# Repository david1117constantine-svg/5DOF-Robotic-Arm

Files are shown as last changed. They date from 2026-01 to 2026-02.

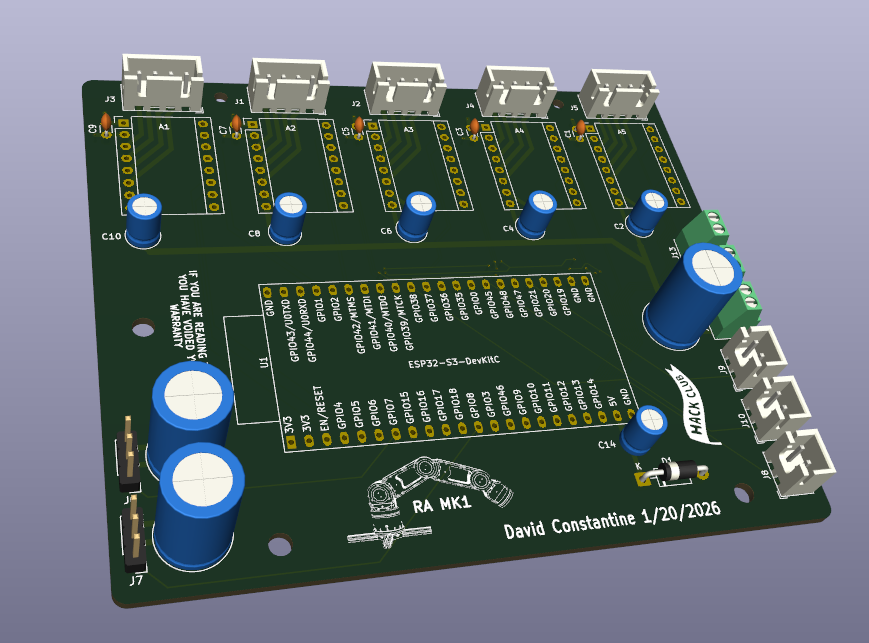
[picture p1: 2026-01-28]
Images/Screenshot 2026-01-27 141930.png

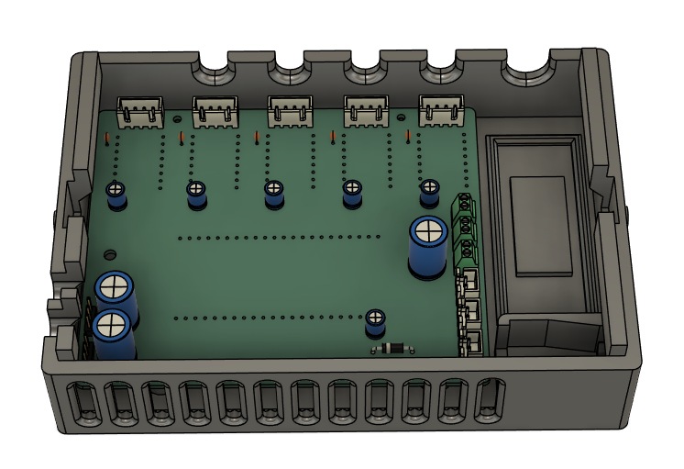
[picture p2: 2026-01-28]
Images/Screenshot 2026-01-28 093712.png

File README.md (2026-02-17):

# 5DOF-Robotic-Arm

This repository is for my very first Hack Club Blueprint Grant Submission, along with anyone else who wants to watch my progress and build their own 5DOF robot arm.



## Overview
* ESP32-S3
* A4988 Drivers
* Nema 17 Stepper Motors
* 25:1 Strain Wave Gearbox *Credit to @user_454693624 over on Makerworld (More Details in CAD Directory)*

## WHY?
This is the first passion project of mine that I have actually pursued. I love engineering, building computers, and 3d printing. All these hobbies have led to this monstrosity of an endeavour. This arm is meant to be modular, easily printable, and fairly inexpensive for hobbyists to build on their own and tinker with. This project has definitely challenged me in ways I couldn't imagine. I started, naive to the oncoming money pit that the thing would become. That's why I am so thankful to the amazing folks over at Blueprint and Hackclub for supporting students in their pursuit of engineering.

## How Does it Work?
This 5DOF Arm is powered by 5 NEMA 17 34mm 0.35A 12V 1.8deg Stepper Motors that you can find at many online stores, such as StepperOnline or, in my case, Adafruit. The joints in the shoulder, elbow, and wrist pitch axis all use the same gearbox and housing assemblies, making for simpler printing and a common attachment point for new structural designs. You might notice there is no end effector piece on this Arm, and that is intentional. The PCB has two servo headers that can be utilized for many different Griper or Claw style designs, or maybe a suction cup or magnet, who knows the possibilities. The PCB is also made for simple installations, simply requiring you to insert your ESP32, motor drivers, servos, etc.

## How To Use It?
One of the major design philosophies behind this project was to build a platform that could be used to test different control mechanisms. As I wrote in the blueprint submission page, I plan to attempt control with a BCI device if I can get my hands on one. To set up the arm, compile and upload the firmware with Arduino IDE, and plug the board into the PCB. I suggest running the code over USB to get a serial output, this will provide you with an IP which you can go to and control the Arm over wifi with the device of your choice. *Note you must replace the SSID and PASSWORD fields with your wifi credentials to let the board connect to wifi. The web GUI is fairly straightforward with multiple ways of interacting with the arm, whether that be individual joint movements or Cartesian Coordinates, though the IK solver has not been refined enough yet for that system to work as intended.

## PCB: Schematic, Footprints, and Renders

#### Schematic:


#### Footprint:


#### Render:


## More Photos:











## BOM
| Item | Quantity | Total Price ($) | Link |
|:---|:---|:---|:---|
| Self-Sourced | | | |
| Screws - Assorted M3 | 2240 | Self-Sourced | |
| Bearing - 6807 2RS | 5 | Self-Sourced | [Link](https://www.amazon.com/XIKE-6807-2RS-Bearings-35x47x7mm-Pre-Lubricated/dp/B09D2ZHNPH/ref=sr_1_4) |
| Microcontroller - ESP32 | 1 | Self-Sourced | [Link](https://www.aliexpress.us/item/3256809776335245.html) |
| Electronics (Exluding PCB) | | | |
| Stepper motor - NEMA-17 size - 200 steps/rev, 12V 350mA | 5 | 70.00 | [Link](https://www.google.com/search?q=NEMA+17+stepper+motor) |
| Stepper Motor Driver - A4988 | 5 | 3.66 | [Link](https://www.aliexpress.us/item/3256808219893938.html) |
| Limit Switch | 3 | 0.41 | [Link](https://www.lcsc.com/product-detail/C50395955.html) |
| Buck Converter - 12v to 5v, 5A | 1 | 2.98 | [Link](https://www.aliexpress.us/item/3256810527502423.html) |
| Wire Connectors - JST xh 2.54 2Pin 10pcs | 1 | 1.39 | [Link](https://www.aliexpress.us/item/3256808413328991.html) |
| Wire Connectors - JST xh 2.54 4Pin 10pcs | 1 | 1.86 | [Link](https://www.aliexpress.us/item/3256808413328991.html) |
| Wire - General Purpose 28 Gauge Wire | 1 | 9.28 | [Link](https://www.aliexpress.us/item/3256805264336680.html) |
| Heat Shrink Tubing - 5mm ID, 5M | 1 | 3.28 | [Link](https://www.aliexpress.us/item/3256806019046145.html) |
| Power Supply - DC12V 8A | 1 | 15.43 | [Link](https://www.aliexpress.us/item/3256801543468653.html) |
| Hardware | | | |
| Extrutions - 150mm 2020 T-slot Extrutions 4pcs | 4 | 18.05 | [Link](https://www.aliexpress.us/item/3256808366074196.html) |
| Screws - M4x10 Countersunk | 4 | 0.02 | [Link](https://jlcmc.com/product/s/E02/EDLJ/din-7991-gb-t-70.3-hex-socket-countersunk-head-screw) |
| Screws - M4x16 BHCS | 8 | 0.09 | [Link](https://jlcmc.com/product/s/E02/EDLG/iso-7380-hex-socket-button-head-screw) |
| T-Nuts - M4 20 Series Profile | 12 | 0.09 | [Link](https://jlcmc.com/product/s/T02/TPAA/m3-m4-m5-t-nut-20-series-aluminum-profile-fasteners) |
| Heat Inserts - M3x4x5 | 100 | 4.18 | [Link](https://www.aliexpress.us/item/3256807712431371.html) |
| NEMA 17 Strain Wave Gearbox (OpenSource) BOM | | | [Link](https://makerworld.com/en/models/1303481-nema-17-strain-wave-gearbox#profileId-1336298) |
| Bearings  - 6706 2RS | 5 | 4.35 | [Link](https://www.aliexpress.us/item/3256806677694798.html) |
| Bearings - 605ZZ | 10 | 0.99 | [Link](https://www.aliexpress.us/item/3256801622664412.html) |
| Bearings - 4mm Balls | 200 | 6.28 | [Link](https://www.aliexpress.us/item/3256807297992129.html) |
| PCB Components | | | |
| Capacitor - 100uF 16V Capacitor | 5 | 0.70 | [Link](https://www.lcsc.com/product-detail/C31190.html) |
| Capacitor - 0.1uF Capacitor | 5 | 0.67 | [Link](https://www.lcsc.com/product-detail/C1620282.html) |
| Capacitor - 47uF | 1 | 0.90 | [Link](https://www.lcsc.com/product-detail/C3540.html) |
| Capacitor - 1000uF | 2 | 1.33 | [Link](https://www.lcsc.com/product-detail/C31154.html) |
| Screw Terminal - 2 Pin | 3 | 1.04 | [Link](https://www.aliexpress.us/item/2251832049646879.html) |
| Schottky Diode - 1N5819 | 2 | 0.06 | [Link](https://www.lcsc.com/product-detail/C2132.html) |
| Female Pin Headers - 1x22 | 2 | 0.80 | [Link](https://www.lcsc.com/product-detail/C474775.html) |
| Female Pin Headers - 1x8 | 10 | 0.59 | [Link](https://www.aliexpress.us/item/3256804116522266.html) |

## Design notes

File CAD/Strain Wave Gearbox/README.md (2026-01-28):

# Credit to user_454693624 over on Makerworld for the Strain-Wave Gearbox design!

### You can find the files for the gearbox design at this link:
https://makerworld.com/en/models/1303481-nema-17-strain-wave-gearbox#profileId-1336298
------
The CAD in this repository contains two modified components of user_454693624's design. First is the Output Hub. I have included this piece in this folder as I needed to extend the hub and change the mounting to threaded inserts. The second modified part is the Cap, which you will find combined in the frames of the Upper Arm, Forearm, and Wrist components.

Again, thank you to user_454693624 for giving me permission to use their design and go check it out!

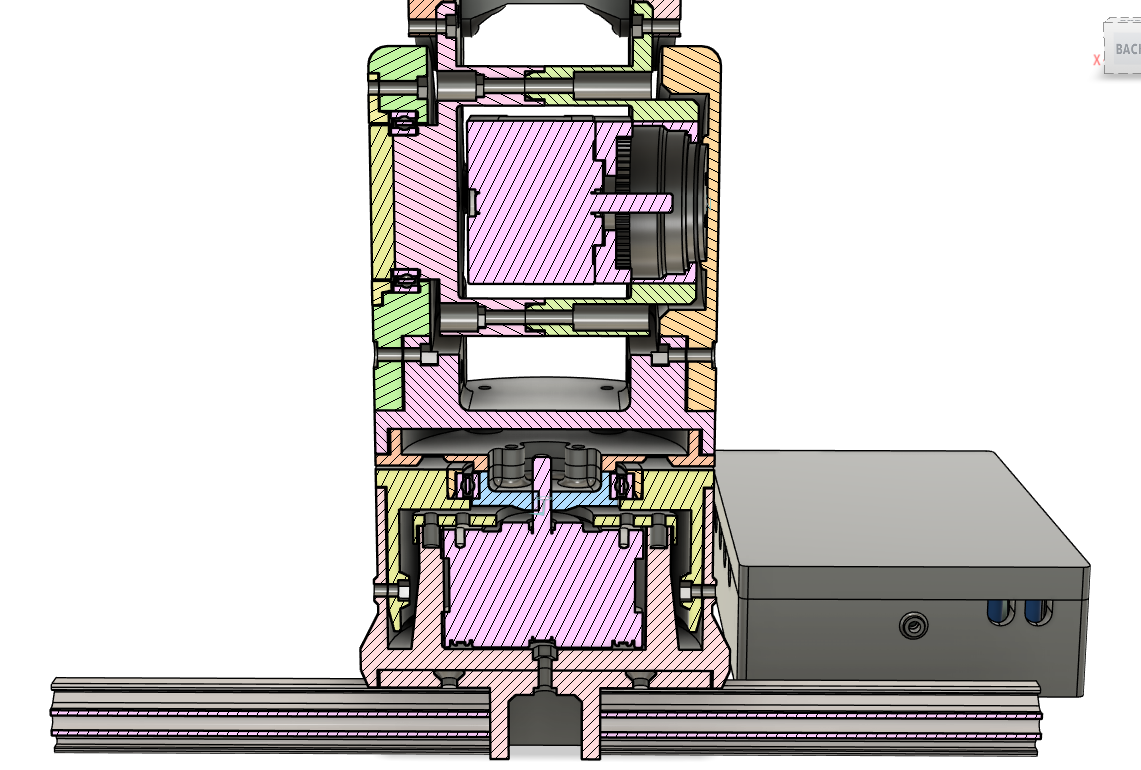
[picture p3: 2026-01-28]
Images/Screenshot 2026-01-28 104803.png

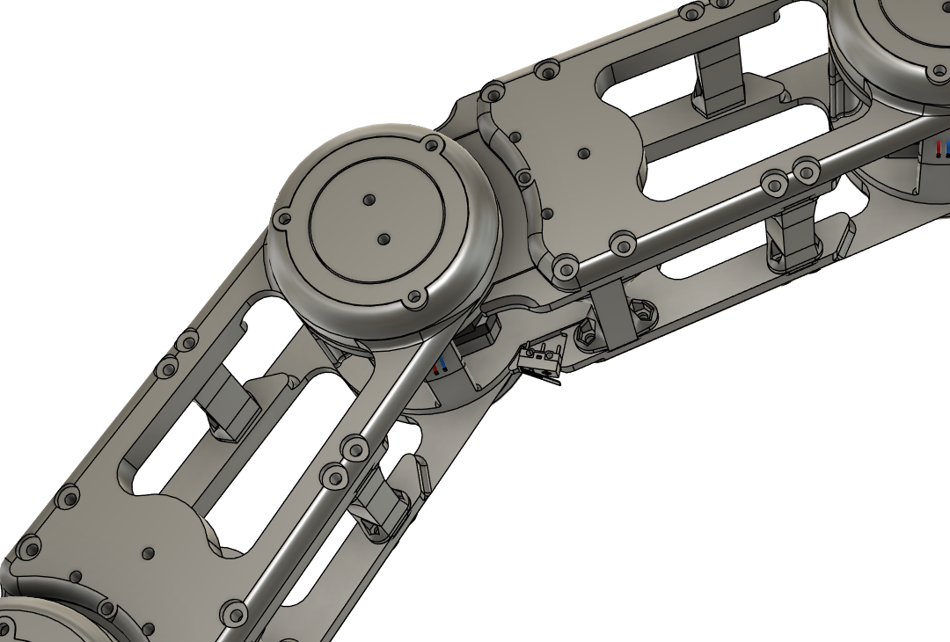
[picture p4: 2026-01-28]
Images/Screenshot 2026-01-28 140131.png

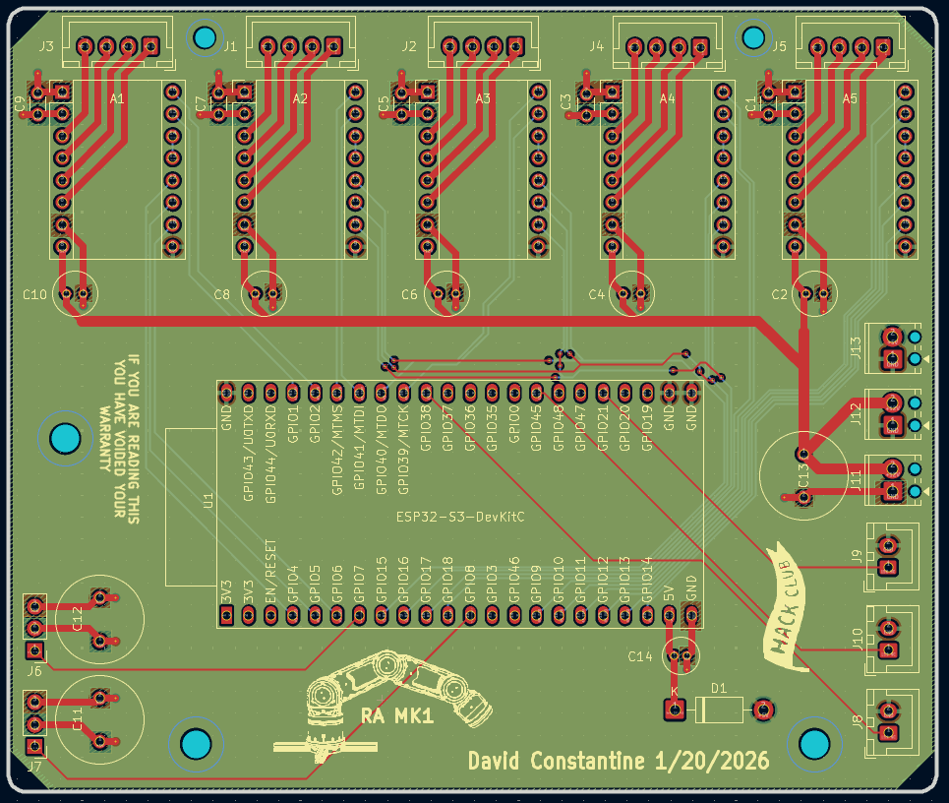
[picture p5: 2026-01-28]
Images/Screenshot 2026-01-27 141817.png

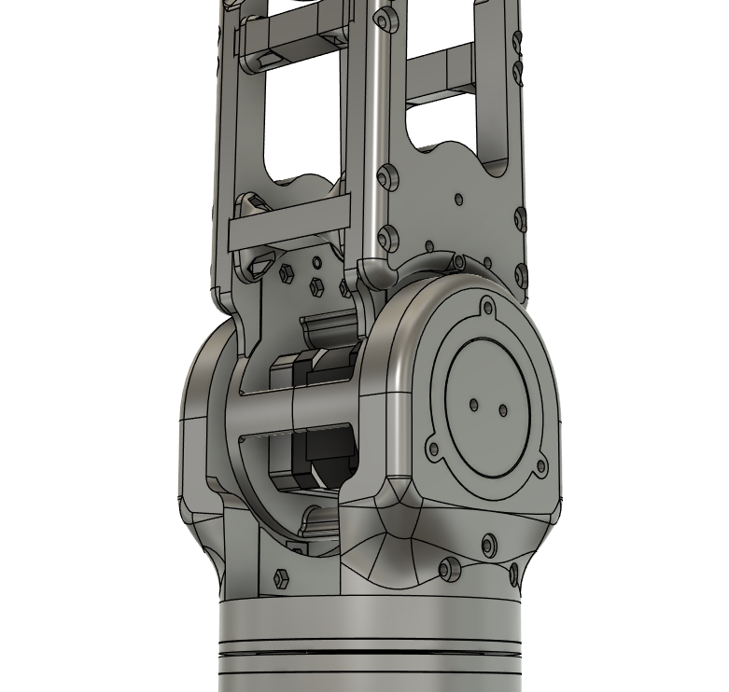
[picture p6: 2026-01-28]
Images/Screenshot 2026-01-28 140021.png

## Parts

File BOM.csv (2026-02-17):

Item | Description | Quantity | Unit Price ($) | Total Price ($) | URL | Running Total ($ with Tax)
Self-Sourced
Screws - Assorted M3 | Screws for general building of the arm, 2440 just came in the box, havent used them all. | 2240 | N/A | Self-Sourced |  | 0.00
Bearing - 6807 2RS | Bearings, 47mm OD, 35mm ID, 7mm Thickness. 6pck on aliexpress seemed to be the cheapest price, though that is on sale so if you are reading this and it is no longer on sale anymore, there is an amazon link with a constant 15.99 price, which I actually sourced. | 5 | N/A | Self-Sourced | https://www.amazon.com/XIKE-6807-2RS-Bearings-35x47x7mm-Pre-Lubricated/dp/B09D2ZHNPH https://www.aliexpress.us/item/3256808547952086.html?curPageLogUid=aeOEVXLjXg1Q | 0.00
Microcontroller - ESP32 | Most ESP32 variants should do as long as they have 36 or more GPIO pins. In this example I am using an ESP32-S3 N18R8 | 1 | N/A | Self-Sourced | https://www.aliexpress.us/item/3256809776335245.html?curPageLogUid=GRDrdkb15ClS | 0.00
Electronics (Exluding PCB)
Stepper motor - NEMA-17 size - 200 steps/rev, 12V 350mA | 4 Wire, 1.8Deg per Step, with 20 N*cm of torque per phase at a max current of 350mAh (0.35A). RoHS certified. | 5 | 14.00 | 70.00 | Stepper motor - NEMA-17 size - 200 steps/rev, 12V 350mA | 75.25
Stepper Motor Driver - A4988 | Stepper Motor Driver, 1.2A, 5 Step resolutions, Adjustable maximum current output. Overheat Thermal shutdown and crossover-current protection. Comes in a pack of 5 for the cheapest sourcing price included both amazon link that had a stable price of 10.19. along with an aliexpress link which often goes on sale for cheaper but can sometimes be 13.95. The price listed is the aliexpress link while on sale | 5 | 0.73 | 3.66 | Amazon.com: A4988 Stepper Motor Driver https://www.aliexpress.us/item/3256808219893938.html?curPageLogUid=ozd9t4rogPcP | 79.18
Limit Switch | Minimum quantity on LCSC was 5, as usual | 3 | 0.08 | 0.41 | https://www.lcsc.com/product-detail/C50395955.html | 79.62
Buck Converter - 12v to 5v, 5A | Buck converter to step down the 12v for the steppers to 5v for the other electronics like the esp and the drivers. | 1 | 2.98 | 2.98 | https://www.aliexpress.us/item/3256810527502423.html?curPageLogUid=wrW3I3VnBbO7 | 82.82
Wire Connectors - JST xh 2.54 2Pin 10pcs | Connectors for the Limit Switches | 1 | 1.39 | 1.39 | https://www.aliexpress.us/item/3256808413328991.html?mp=1 | 84.31
Wire Connectors - JST xh 2.54 4Pin 10pcs | Connectors for the steppers, will allow for much easier building and protoyping | 1 | 1.86 | 1.86 | https://www.aliexpress.us/item/3256808413328991.html?mp=1 | 86.31
Wire - General Purpose 28 Gauge Wire | Wire for extention cables for the Stepper Motors | 1 | 9.28 | 9.28 | https://www.aliexpress.us/item/3256805264336680.html | 96.29
Heat Shrink Tubing - 5mm ID, 5M | For all the soldered joints to be electrically insulated | 1 | 3.28 | 3.28 | https://www.aliexpress.us/item/3256806019046145.html?mp=1 | 99.82
Power Supply - DC12V 8A | Power Supply for the arm | 1 | 15.43 | 15.43 | https://www.aliexpress.us/item/3256801543468653.html?mp=1 | 116.41
Hardware
Extrutions - 150mm 2020 T-slot Extrutions 4pcs | Extrutions for the base of the arm. Will allow for the arm to be mounted almost anywhere or stand alone when the end effector is within a certain radius. | 4 | 4.51 | 18.05 | https://www.aliexpress.us/item/3256808366074196.html?curPageLogUid=zHtV8X7rHrXA | 135.81
Screws - M4x10 Countersunk | Countersunk M4 screws for connecting the extrutions to Robot Base | 4 | 0.0043 | 0.02 | https://jlcmc.com/product/s/E02/EDLJ/din-7991-gb-t-70.3-hex-socket-countersunk-head-screw | 135.83
Screws - M4x16 BHCS | BHCS M4 screws for connecting the extrutions to the base | 8 | 0.0111 | 0.09 | https://jlcmc.com/product/s/E02/EDLG/iso-7380-hex-socket-button-head-screw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 | 135.93
T-Nuts - M4 20 Series Profile | T-Nuts for connecting extrutions to robot base | 12 | 0.0075 | 0.09 | https://jlcmc.com/product/s/T02/TPAA/m3-m4-m5-t-nut-20-series-aluminum-profile-fasteners | 136.03
Heat Inserts - M3x4x5 | Need some more for the design | 100 | 0.0418 | 4.18 | https://www.aliexpress.us/item/3256807712431371.html?curPageLogUid=NFashz8ytky9 | 140.52
NEMA 17 Strain Wave Gearbox (OpenSource) BOM |  |  |  |  | https://makerworld.com/en/models/1303481-nema-17-strain-wave-gearbox#profileId-1336298
Bearings - 6706 2RS |  | 5 | 0.87 | 4.35 | https://www.aliexpress.us/item/3256806677694798.html?curPageLogUid=v6HSvHcuK7CU | 145.20
Bearings - 605ZZ |  | 10 | 0.1 | 0.99 | https://www.aliexpress.us/item/3256801622664412.html?curPageLogUid=edU8vGmWTP8q | 146.26
Bearings - 4mm Balls |  | 200 | 0.0314 | 6.28 | https://www.aliexpress.us/item/3256807297992129.html?curPageLogUid=DUdxTNKNhLz3 | 153.01
PCB Components
Capacitor - 100uF 16V Capacitor | Minimum quantity was 50 on LCSC | 5 | 0.014 | 0.70 | https://www.lcsc.com/product-detail/C2960196.html?s_z=n_100uf%2520capacitor | 153.76
Capacitor - 0.1uF Capacitor | Minimum quantity was 5 on LCSC | 5 | 0.1347 | 0.67 | https://www.lcsc.com/product-detail/C1620282.html | 154.48
Capacitor - 47uF | Comes in 20pcs on Aliexpress, cheaper than LCSC surprisingly | 1 | 0.045 | 0.90 | https://www.aliexpress.us/item/3256804117722266.html?curPageLogUid=qXib9S2fzA2W | 155.45
Capacitor - 1000uF | Comes in 20pcs on Aliexpress, couldnt find on LCSC | 2 | 0.0665 | 1.33 | https://www.aliexpress.us/item/3256804117722266.html?curPageLogUid=qXib9S2fzA2W | 156.88
Screw Terminal - 2 Pin | Comes in 5pcs on Aliexpress | 3 | 0.208 | 1.04 | https://www.aliexpress.us/item/3256807006502215.html?curPageLogUid=ZN9fxmU7svuY | 158.00
Schottky Diode - 1N5819 | Got 2 because knowing me I'm gonna break one soldering | 2 | 0.03 | 0.06 | https://www.lcsc.com/product-detail/C2906661.html | 158.06
Female Pin Headers - 1x22 | For the ESP32 | 2 | 0.4014 | 0.80 | https://www.lcsc.com/product-detail/C20071202.html | 158.92
Female Pin Headers - 1x8 | For A4988 Drivers | 10 | 0.0585 | 0.59 | https://www.lcsc.com/product-detail/C429957.html | 159.55

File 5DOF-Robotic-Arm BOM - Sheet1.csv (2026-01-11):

Item | Description | Quantity | Unit Price ($) | Total Price ($) | URL | Running Total ($ with Tax)
Bearing - 6807 2RS | Bearings, 47mm OD, 35mm ID, 7mm Thickness. 6pck on aliexpress seemed to be the cheapest price, though that is on sale so if you are reading this and it is no longer on sale anymore, there is an amazon link with a constant 15.99 price, which I actually sourced. | 5 | N/A | Self-Sourced | https://www.amazon.com/XIKE-6807-2RS-Bearings-35x47x7mm-Pre-Lubricated/dp/B09D2ZHNPH https://www.aliexpress.us/item/3256808547952086.html?curPageLogUid=aeOEVXLjXg1Q | 0.00
Microcontroller - ESP32 | Most ESP32 variants should do as long as they have 36 or more GPIO pins. In this example I am using an ESP32-S3 N18R8 | 1 | N/A | Self-Sourced | https://www.aliexpress.us/item/3256809776335245.html?curPageLogUid=GRDrdkb15ClS | 0.00
Stepper motor - NEMA-17 size - 200 steps/rev, 12V 350mA | 4 Wire, 1.8Deg per Step, with 20 N*cm of torque per phase at a max current of 350mAh (0.35A). RoHS certified. | 5 | 14.00 | 70.00 | Stepper motor - NEMA-17 size - 200 steps/rev, 12V 350mA | 75.25
Stepper Motor Driver - A4988 | Stepper Motor Driver, 1.2A, 5 Step resolutions, Adjustable maximum current output. Overheat Thermal shutdown and crossover-current protection. Comes in a pack of 5 for the cheapest sourcing price included both amazon link that had a stable price of 10.19. along with an aliexpress link which often goes on sale for cheaper but can sometimes be 13.95. The price listed is the aliexpress link while on sale | 5 | 1.18 | 5.90 | Amazon.com: A4988 Stepper Motor Driver https://www.aliexpress.us/item/3256808219893938.html?curPageLogUid=ozd9t4rogPcP | 81.59
Buck Converter - 12v to 5v | Buck converter to step down the 12v for the steppers to 5v for the other electronics like the esp and the drivers. | 1 | 1.69 | 1.69 | https://www.aliexpress.us/item/3256805964919227.html?curPageLogUid=Vf5B1UHJQ9oe | 83.41
Wire Connectors - JST xh 2.54 5Pin 10pcs | Connectors for the steppers, will allow for much easier building and protoyping | 1 | 2.31 | 2.31 | https://www.aliexpress.us/item/3256808501357728.html?curPageLogUid=yp1VBhINy1jJ | 85.89
Power Supply - DC12V 5A | Power Supply for the arm. Comes with EU plug, but I have so many C14 power cables it isnt funny. Should not be a problem. | 1 | 8.32 | 8.32 | https://www.aliexpress.us/item/3256810479010704.html?curPageLogUid=Aaaj8G0MkgZc | 94.83
Extrutions - 150mm 2020 T-slot Extrutions 4pcs | Extrutions for the base of the arm. Will allow for the arm to be mounted almost anywhere or stand alone when the end effector is within a certain radius. | 1 | 17.96 | 17.96 | https://www.aliexpress.us/item/3256808366074196.html?curPageLogUid=zHtV8X7rHrXA | 114.14
Screws - M4x10 Countersunk | Countersunk M4 screws for connecting the extrutions to Robot Base | 4 | 0.0043 | 0.02 | https://jlcmc.com/product/s/E02/EDLJ/din-7991-gb-t-70.3-hex-socket-countersunk-head-screw | 114.16
Screws - M4x16 BHCS | BHCS M4 screws for connecting the extrutions to the base | 8 | 0.0111 | 0.09 | https://jlcmc.com/product/s/E02/EDLG/iso-7380-hex-socket-button-head-screw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 | 114.26
T-Nuts - M4 20 Series Profile | T-Nuts for connecting extrutions to robot base | 12 | 0.0075 | 0.09 | https://jlcmc.com/product/s/T02/TPAA/m3-m4-m5-t-nut-20-series-aluminum-profile-fasteners | 114.36
Wire - General Purpose 28 Gauge Wire | Wire for extention cables for the Stepper Motors | 1 | 9.66 | 9.66 | https://www.aliexpress.us/item/3256805264336680.html | 124.74
Sweep Dynamics Cycloidal BOM
Bearings - 6707 2RS |  | 10 | 1.97 | 19.75 | https://www.aliexpress.us/item/2255800723290638.html | 145.97
Bearings - MR137ZZ |  | 10 | 0.93 | 9.29 | https://www.amazon.com/uxcell-Miniature-Bearings-Appliances-Machinery/dp/B0D2LBCKP2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 | 155.96
Bearings - MR128 2RS |  | 10 | 1.00 | 10.01 | https://www.aliexpress.us/item/3256806709867700.html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 | 166.72
Rollers - M3x5mmx10mm | Only need 30 ordering 40 is cheapest | 40 | 0.22 | 8.78 | https://www.aliexpress.us/item/3256805776299657.html | 176.16
Screws - M3x20 BHCS |  | 30 | 0.0082 | 0.25 |  | 176.42
Screws - M3x8 Countersunk |  | 20 | 0.0032 | 0.06 |  | 176.49

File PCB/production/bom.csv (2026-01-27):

Designator | Footprint | Quantity | Value | LCSC Part #
A1, A2, A3, A4, A5 | Pololu_Breakout-16_15.2x20.3mm | 5 | Breakout_A4988
C1, C3, C5, C7, C9 | C_Disc_D3.0mm_W1.6mm_P2.50mm | 5 | 100nF
C10, C2, C4, C6, C8 | C_Radial_D5.0mm_H7.0mm_P2.00mm | 5 | 100uF
C11, C12, C13 | C_Radial_D10.0mm_H16.0mm_P5.00mm | 3 | 1000uF
C14 | C_Radial_D4.0mm_H7.0mm_P1.50mm | 1 | 47uF
D1 | D_DO-41_SOD81_P10.16mm_Horizontal | 1 | 1N5819
J1, J2, J3, J4, J5 | JST_XH_B4B-XH-A_1x04_P2.50mm_Vertical | 5 | JST XH 2.54 4Pin
J10 | JST_XH_B2B-XH-A_1x02_P2.50mm_Vertical | 1 | LS3
J11 | TerminalBlock_Phoenix_MPT-0,5-2-2.54_1x02_P2.54mm_Horizontal | 1 | 12Vin
J12 | TerminalBlock_Phoenix_MPT-0,5-2-2.54_1x02_P2.54mm_Horizontal | 1 | 12Vout
J13 | TerminalBlock_Phoenix_MPT-0,5-2-2.54_1x02_P2.54mm_Horizontal | 1 | 5Vin
J6 | PinHeader_1x03_P2.54mm_Vertical | 1 | Servo 1
J7 | PinHeader_1x03_P2.54mm_Vertical | 1 | Servo 2
J8 | JST_XH_B2B-XH-A_1x02_P2.50mm_Vertical | 1 | LS1
J9 | JST_XH_B2B-XH-A_1x02_P2.50mm_Vertical | 1 | LS2
U1 | ESP32-S3-DevKitC | 1 | ESP32-S3-DevKitC

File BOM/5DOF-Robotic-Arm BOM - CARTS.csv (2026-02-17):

Store/Website | Total | Shipping | Grand Total | Notes
JLCPC/JLCMC | $29.19 | $10.11 | $39.30
LCSC | $3.38 | $9.05 | $15.39 | Extra Fees: 3.00 Handling Fee + 0.04 discount?
AliExpress | $77.04 | $37.67 | $123.33 | Extra Fees: 8.62
Digikey | $70.00 | $6.99 | $76.99
 |  |  | $255.01

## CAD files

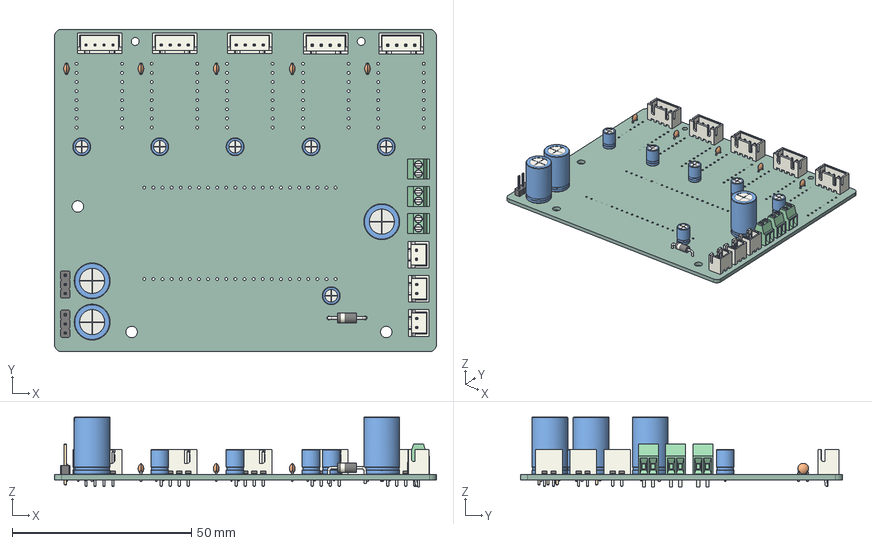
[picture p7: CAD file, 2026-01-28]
CAD/Electronics/5DOF-Robotic-Arm-PCB_MK2.5.step
106.5 x 89.9 x 19.5 mm
C_Disc_D3.0mm_W1.6mm_P2.50mm x 5
C_Radial_D10.0mm_H16.0mm_P5.00mm x 3
C_Radial_D5.0mm_H7.0mm_P2.00mm x 5
JST_XH_B4B-XH-A_1x04_P2.50mm_Vertical x 5
D_DO-41_SOD81_P10.16mm_Horizontal
TerminalBlock_Phoenix_MPT-0,5-2-2.54_1x02_P2.54mm_Horizontal x 3
JST_XH_B2B-XH-A_1x02_P2.50mm_Vertical x 3
PinHeader_1x03_P2.54mm_Vertical x 2
C_Radial_D4.0mm_H7.0mm_P1.50mm
5DOF-Robotic-Arm-PCB_MK2_PCB

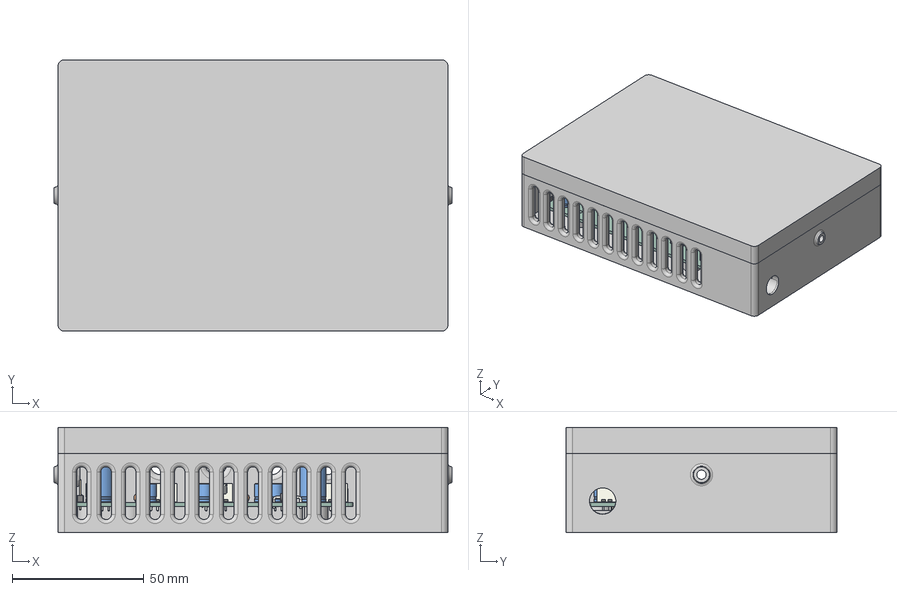
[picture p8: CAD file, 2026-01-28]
CAD/Electronics/Electronics Case/Electronics Case.step
151.0 x 103.0 x 40.0 mm
DC Barrel to Screw Terminal Adapter Fit Test
Electronics_Case
C_Disc_D3.0mm_W1.6mm_P2.50mm x 5
C_Radial_D10.0mm_H16.0mm_P5.00mm x 3
C_Radial_D5.0mm_H7.0mm_P2.00mm x 5
JST_XH_B4B-XH-A_1x04_P2.50mm_Vertical x 5
D_DO-41_SOD81_P10.16mm_Horizontal
TerminalBlock_Phoenix_MPT-0,5-2-2.54_1x02_P2.54mm_Horizontal x 3
JST_XH_B2B-XH-A_1x02_P2.50mm_Vertical x 3
PinHeader_1x03_P2.54mm_Vertical x 2
C_Radial_D4.0mm_H7.0mm_P1.50mm
5DOF-Robotic-Arm-PCB_MK2_PCB
Electronics_Case_Lid

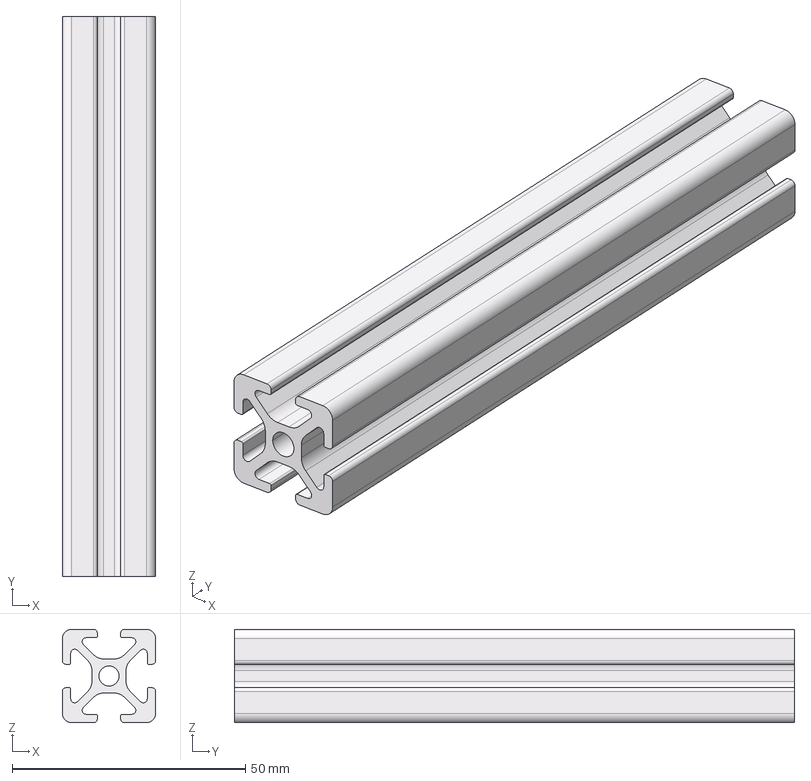
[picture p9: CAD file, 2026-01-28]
CAD/Extrution/item_37003_profile-5-20x20-natural-_120_high.step
20.0 x 120.0 x 20.0 mm

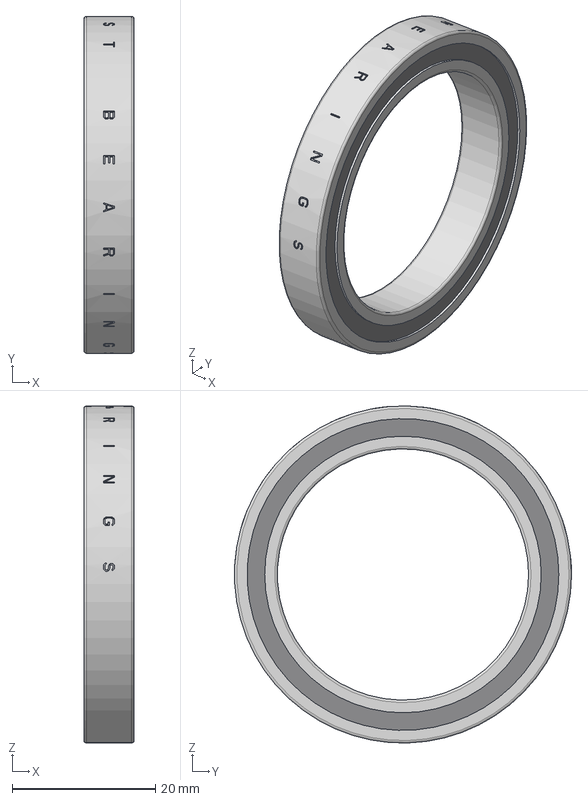
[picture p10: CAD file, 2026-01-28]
CAD/Misc Parts/AST_Bearings_6807-2RS.step
7.01 x 47.0 x 47.0 mm

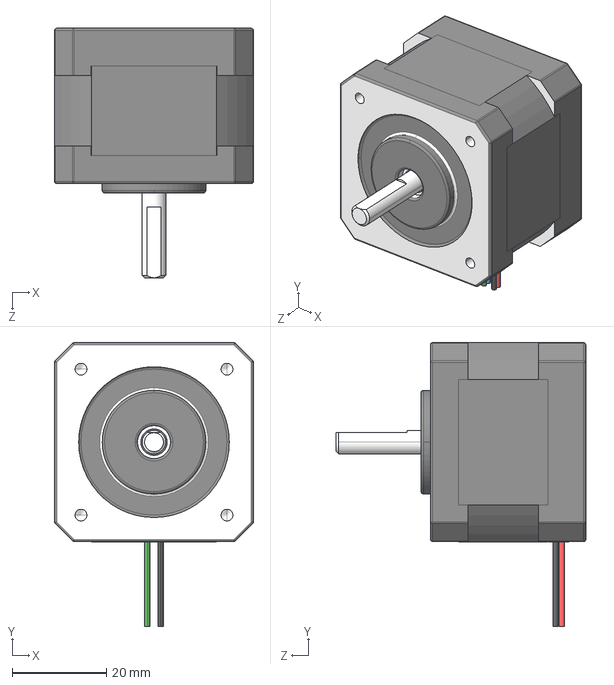
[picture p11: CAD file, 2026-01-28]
CAD/Nema 17 Motor/17HS13-0404S1.STEP
42.3 x 60.3 x 53.0 mm

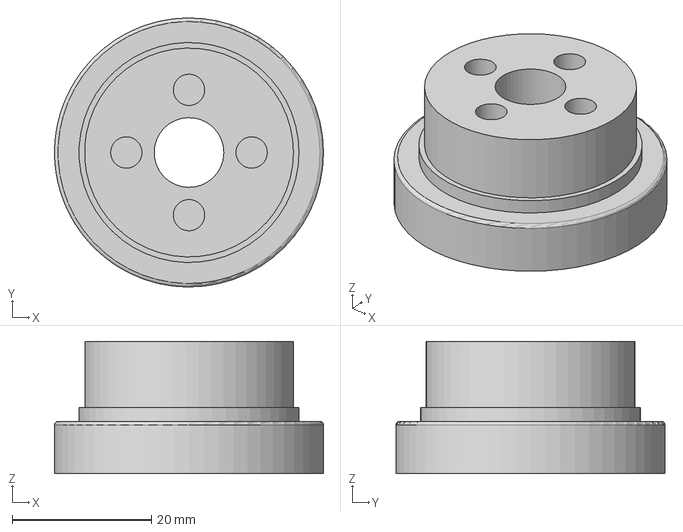
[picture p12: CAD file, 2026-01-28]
CAD/Strain Wave Gearbox/Output Hub.step
38.6 x 38.6 x 19.0 mm

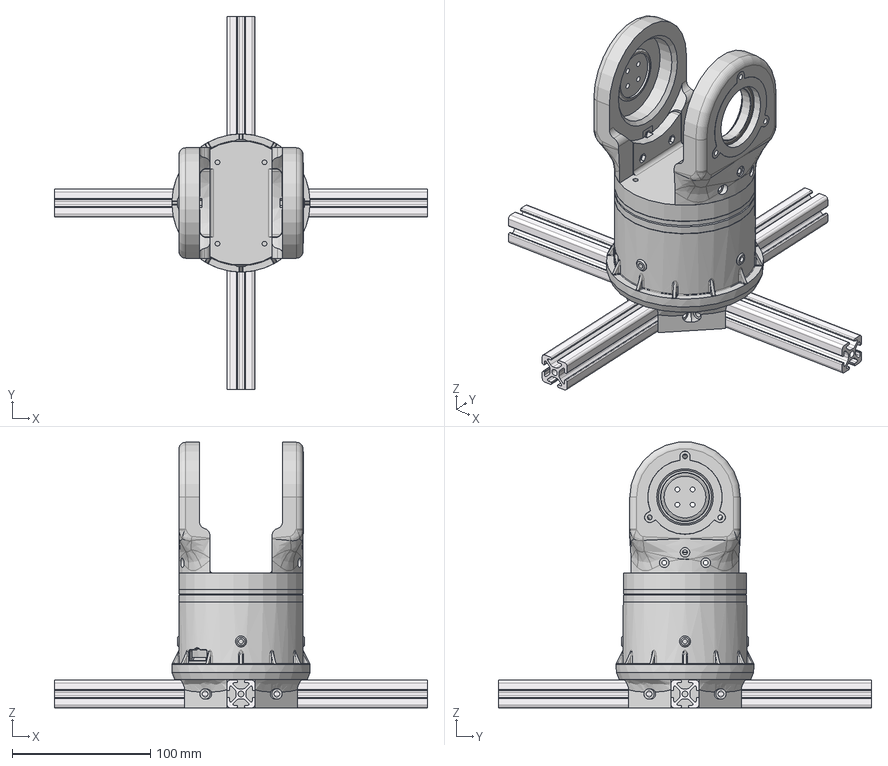
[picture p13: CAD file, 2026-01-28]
CAD/Waist + Shoulder/Robotic_Arm-Waist+Shoulder.step
270.0 x 270.0 x 192.3 mm
item_0037003_Profil 5 20x20_L=120_1 x 4
Base_ExtrusionConectors
Waist_Floor-Motor_Cap
Waise_FloorBearingCap
6807-2RS x 2
Waist_BearingTentionRing
Hip_WaistBeaaringBottom
Hip_WaistPlate
Hip_Hip-Arm_Base
Hip_Hip-Arm_Bearing-Arm
Hip_Hip-Arm_Bearing_Cover
Hip_Hip-Arm_Gear_Arm
17HS13-0404S1

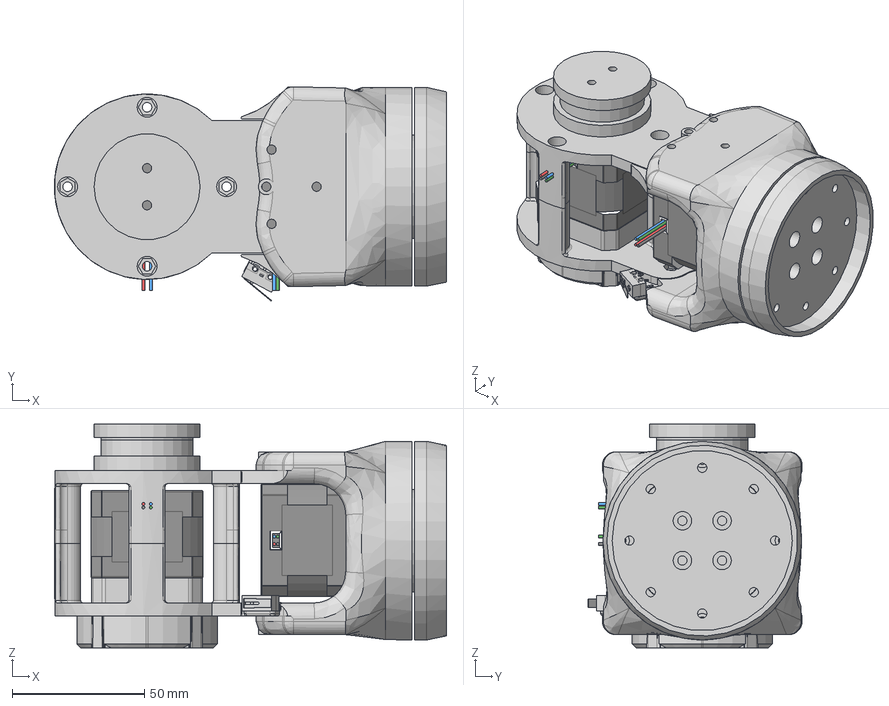
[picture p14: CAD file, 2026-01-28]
CAD/Wrist/Robotic_Arm-Wrist.step
147.9 x 80.9 x 84.5 mm
Cap
Upper_Arm-Bearingside
Upper_Arm-Bearing_Cover
Fixed Stator
17HS13-0404S1 x 2
Wrist_Frame
6807-2RS
Wrist_Bearing_Cap
Wrist_Rear_Bearing_Cap
Wrist_End_Effector_Mount
000021319_Simplify_1

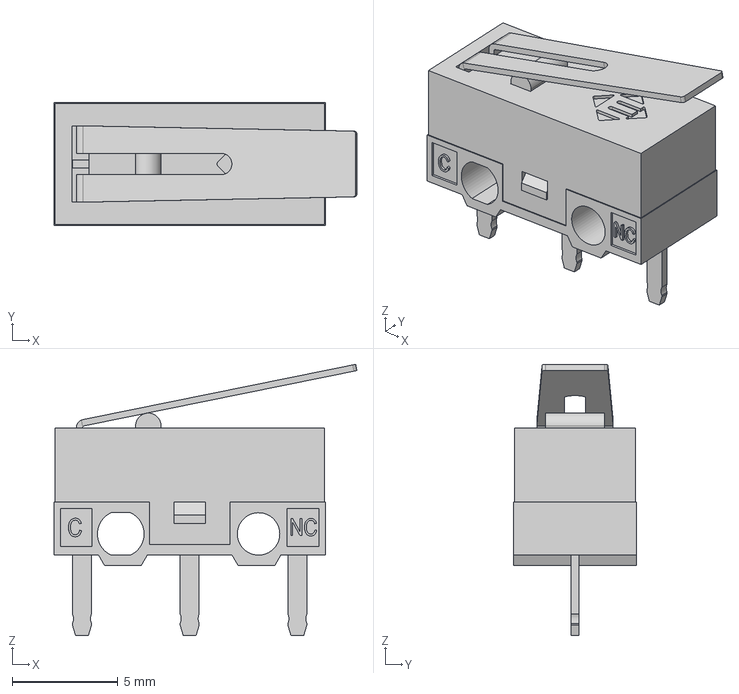
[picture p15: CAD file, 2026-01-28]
CAD/Misc Parts/SS075xx01FxxxP1A.step
14.3 x 5.80 x 12.8 mm

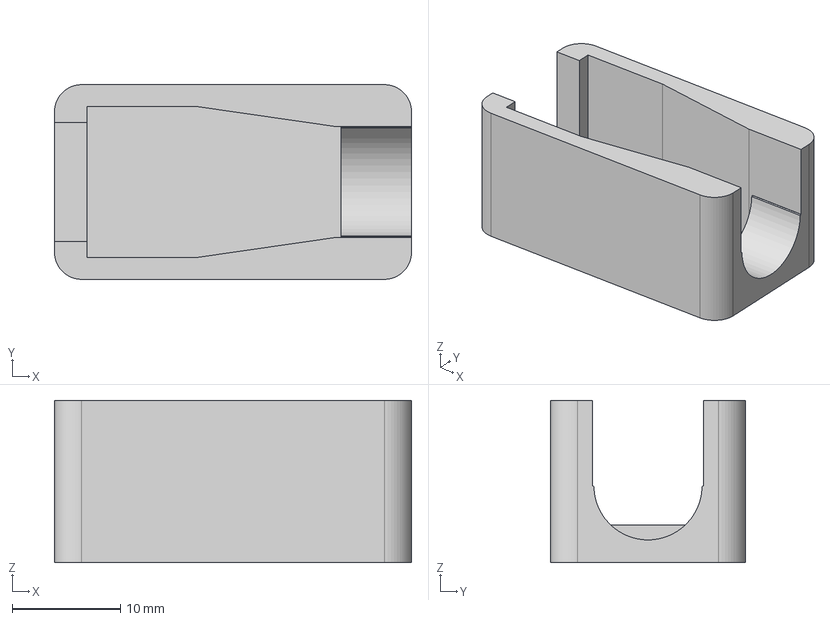
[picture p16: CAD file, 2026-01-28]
CAD/Electronics/Barrel to Screw Terminal Adapter Fit/DC Barrel to Screw Terminal Adapter Fit Test.step
33.0 x 18.0 x 15.0 mm

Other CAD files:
CAD/Electronics/Barrel to Screw Terminal Adapter Fit/DC Barrel to Screw Terminal Adapter Fit Test.f3d
CAD/Electronics/Electronics Case/Electronics Case.f3z
CAD/Forearm/Robotic_Arm-Forearm_Lite.f3z
CAD/Strain Wave Gearbox/Output Hub.f3d
CAD/Upper Arm/Robotic_Arm-Upper_Arm_Lite.f3z
CAD/Waist + Shoulder/Robotic_Arm-Waist+Shoulder.f3z
CAD/Wrist/Robotic_Arm-Wrist.f3z

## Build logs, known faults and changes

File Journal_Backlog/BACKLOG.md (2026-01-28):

# Journal Backlog: October 24th, 2025 - January 8th 2026

## 1/8/2026: Instagram to the rescue?
I was scrolling through Instagram today, as you do, and I saw a reel with a guy talking about how teens can get funding for hardware projects through a program called Blueprint. I think I had seen this before, but only remembered it being with macropads, but apparently not. Ive got nothing to loose so maybe I'll apply for that and see where it leads?

## 1/4/2026: Upper Arm Prototype complete; My suspisions were correct.
I completed the Upper Arm and did some tests. It seems to lose about 5 degrees from skipping when trying to lift itself from the edges of its range of motion, about 70 degrees in either direction.



At this point, I think this project is going to have to be put on a shelf till I can scrounge up sufficient funding to get some NEMA 17 motors or something similar. Ive already put just over 100 dollars into it, not including filament cost, and its prooving to be a money pit. Unless I get a crazy influx of work or gifts im not sure what I'll do.

## 1/2/2026: 28BYJ-48's Gotta go, is the project done for?
A lot happened over New Year's. I designed an upper arm prototype and got it printed on the Ender. Thank goodness I got that cause these parts were pretty big and took all day. Here are some photos of half assembled, the other side was still printing:









You can see where I test printed the mount out on the voron so I wouldn't waste filament if it didn't fit, and thank goodness I did because I had goofed on a pin placement. I also designed some struts to go between both halves of the upper arm's frame, and those are currently on the Voron. I fear that once I test the movement of the shoulder joint with the Upper Arm fully assembled, it may be able to lift itself, but nowhere near enough torque to lift anything like this render.



## 12/30/2025: Ive done it once, I'll do it again... Redesign time!
The initial Upper arm design I've been visualizing in my head is simply far too heavy to even stand a chance of realistically working. Im now going for something almost opposite, a skeleton design. The arm is going to look bare bones, but it will be lighter, maybe even stronger, and pretty easy to prototype with. Plus, saving filament is always a bonus. Ive designed a new piece that fits in the shoulder and consists of two disks connected with 4, strut-like pillars keeping them together. The pillars have holes running all the way through and can be screwed together with M3x25 screws and nuts. After I confirmed all the dimensions with a test print, I added an interface to build the Upper Arm's frame off of. Here's what it looks like in CAD: 



## 12/24/2025: Its Christmas Eve, and the first iteration of the Upper Arm mount to the shoulder. 
Prototype? The goal is to have everything internalized so the outside looks super clean. I ran into a ton of issues with jamming the entire motor assembly into the casing. It still doesn't totally fit, but I put the newest version together,r and I can definitely see the vision. 



I have been using a little script I wrote that can use serial commands to control a single motor, and the shoulder does move, but with much difficulty. Weight seems like it will be an issue, but until then, that is where I'm at.

## 12/22/2025: Holidays are ramping up, and so am I.
Finally printed the last of the shoulder pieces. Took a few iterations; the first time, I didn't even include all the holes for the screws; too excited, I guess.





Forgot to mention in the last entry that the gear-like hole in the motor side of the shoulder is for the output shaft of a simple planetary gearbox design I found on printables. *(Future me wants to add I did not go with this design, but it's a combination of ProfessorBoots' 4:1 planetary gearboxes and @flolorenzo's 28BYJ48 motor adapter)* One 4:1 gearbox is not enough, according to my calculations, but thankfully, this design is stackable, so I went with two gearboxes, totalling a 16:1 reduction.



## 12/15/2025: Shouler redesign went quite painlessly; lets hope I didnt just jinx anything!
The new design features what I outlined in the previous entry: removable shoulder arms to allow for easier assembly, one simple loft instead of some really jacked-up ones like in the previous design, and now one side has a groove for a toothed shaft to fit into, allowing the arm to actually turn.



## 12/11/2025: CAD sucks, and I'm restarting the shoulder. (Lofts are the bane of my existence)

Been working on the shoulder the past couple of days, finally got something that I was kind of proud of. 



Honestly, it doesn't look that bad; it isn't that bad, except for a few obvious flaws. First, you will notice that both sides of the shoulder mount have cuts for bearings to sit in. If there are bearings on either side, how is the Upper arm supposed to move? The second major flaw is with the physical construction of the shoulder joint. I think I am going to start over and move towards a design in which I can remove either side of the Shoulder mount arm thingies to aid in assembly. When both sides are fixed, you would basically have to bend them in order to squeeze something into the middle, unless you ran some sort of rod inbetween but I don't think I'm gonna do that.

## 12/4/2025: New Printer!
Just got a new 3d printer that's gonna help in printing all the larger pieces of the arm! It's a Creality Ender 3 S1, and it was broken when a friend gave it to me, but it only took about 20 minutes to fix the software issues, just reflashed the firmware, and it whirred to life.





## 12/1/2025: The Waist Continues!!!
Started printing the next couple of pieces. The inside of the waist is closed off with a type of cap, which also has a tray on top for the bearing to sit in and be screwed into place. 





## 11/30/2025: Locking in; Waist progressing smoothly
I decided to start building the arm around these cheap stepper motors I found in my school's computer lab, specifically the 28-BYJ-48 with ULN2003 drivers. They seem pretty cheap, so that is good for my budget, which is basically nothing. Added the ribbing on the side for effect, looks cool, I think, and maybe it provides marginal support theoretically. Using little holes i measured out that you can pop nuts into, and then you get threads, cheaper and more accessible than heatset inserts; also less permanent. The only hardware I have right now is what is left from the 3D printer build. It won't last me the entire build, but for now, it will have to do.





You may be able to see a little bit of material that sticks out around the screw holes in the motor mount. This began by accident; however turned out that it works in my favor. The mounting holes on the 28BYJ-48 steppers are for M4 screws; however, the only screws I have on hand are M3. The M3 screws thread into the plastic, which in turn squeezes the raised material outward, centering the motor over the screw holes, and squeezing them tight onto the posts. Cool right?



Cool design feature I should mention. For now, I am sticking with the extrusions for a simple solution to a base/mount for the arm. I designed the waist with the idea of multiple mounting options in mind. There is an X pattern of crews and a circular depression in the bottom of the waist, allowing it to be connected to many mounting solutions. Still brainstorming how the actual waist joint is going to stay in place, planning on buying bearings of some sort for the spinning aspect, but we will see, I guess.

Here it is on the printer, complete, I might add.



## 11/29/2025: Tuning, Tuning, Tuning; Ready to print 1st part of the Arm!
Designed a base piece that would connect the extrusions and bolt onto whatever the design for the Waise Joint will be. The first print came out fine, needed some clearance fixes though, went back into cad and it's all good now!






This was the 1st version, which was missing drilled holes for connecting the waist, along with too loose clearances.


V2 on the Voron

## 11/16/2025: Voron is done, first print is out of the way; Back to CAD!
Did some thinking about my previous design, and I think I'm gonna scratch the entire thing and start over. Gonna use 2020 extrusions along, and start from there.



## 10/25/2025: Last of the Voron parts came; Project on standby for now
Not much to this entry. I'm super excited to finally have a 3D printer again. I need to find a place to keep all the different benchys I'm about to make!

## 10/24/2025: The Birth of an Idea
Yesterday I got my new Voron V0.2 in the mail! Decided to start modeling the glimpse of an idea I saw in my head of a Robotic Arm, built all with hobby-grade 3D printing. Looks pretty trash right now, but I think with some work it should be ok. I've got a lot to learn about Fusion 360 still, so this is probably good for me. using 4040 extrusions for the base, hopefully that is a wide and sturdy enough structure to hold the arm up. Thats all I've got for now!



P.S. Sorry for the terrible quality image; it was a screenshot from my phone.

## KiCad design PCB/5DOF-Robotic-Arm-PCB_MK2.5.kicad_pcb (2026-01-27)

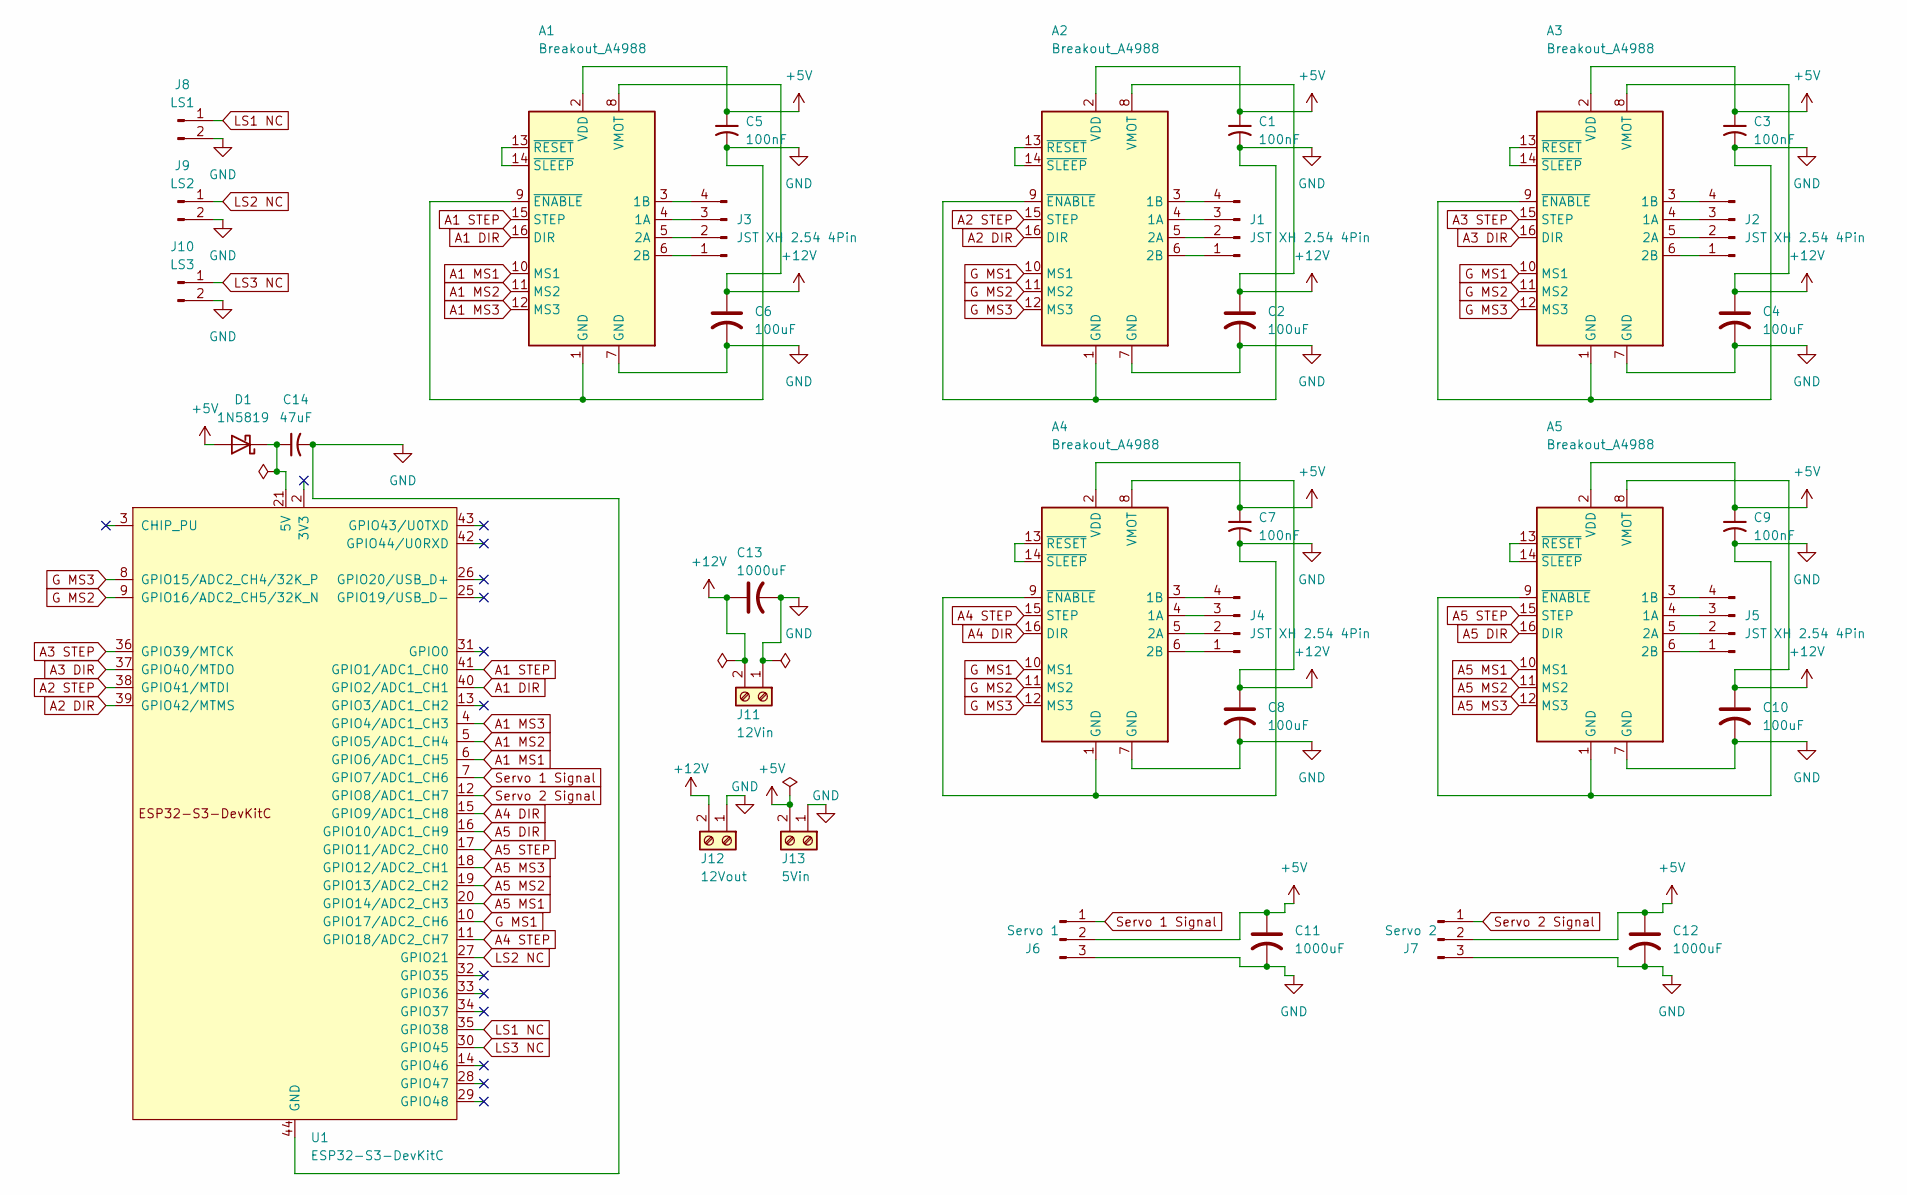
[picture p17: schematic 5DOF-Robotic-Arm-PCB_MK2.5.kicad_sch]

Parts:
A1, A2, A3, A4, A5: Breakout_A4988; Pololu_Breakout-16_15.2x20.3mm
C1, C3, C5, C7, C9: 100nF; C_Disc_D3.0mm_W1.6mm_P2.50mm
C2, C4, C6, C8, C10: 100uF; C_Radial_D5.0mm_H7.0mm_P2.00mm
C11, C12, C13: 1000uF; C_Radial_D10.0mm_H16.0mm_P5.00mm
C14: 47uF; C_Radial_D4.0mm_H7.0mm_P1.50mm
D1: 1N5819; D_DO-41_SOD81_P10.16mm_Horizontal
J1, J2, J3, J4, J5: JST XH 2.54 4Pin; JST_XH_B4B-XH-A_1x04_P2.50mm_Vertical
J6: Servo 1; PinHeader_1x03_P2.54mm_Vertical
J7: Servo 2; PinHeader_1x03_P2.54mm_Vertical
J8: LS1; JST_XH_B2B-XH-A_1x02_P2.50mm_Vertical
J9: LS2; JST_XH_B2B-XH-A_1x02_P2.50mm_Vertical
J10: LS3; JST_XH_B2B-XH-A_1x02_P2.50mm_Vertical
J11: 12Vin; TerminalBlock_Phoenix_MPT-0,5-2-2.54_1x02_P2.54mm_Horizontal
J12: 12Vout; TerminalBlock_Phoenix_MPT-0,5-2-2.54_1x02_P2.54mm_Horizontal
J13: 5Vin; TerminalBlock_Phoenix_MPT-0,5-2-2.54_1x02_P2.54mm_Horizontal
U1: ESP32-S3-DevKitC

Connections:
+5V: A1.2 (VDD), A2.2 (VDD), A3.2 (VDD), A4.2 (VDD), A5.2 (VDD), C1.1, C3.1, C5.1, C7.1, C9.1, C11.1, C12.1, D1.2 (A), J6.2, J7.2, J13.2
+12V: A1.8 (VMOT), A2.8 (VMOT), A3.8 (VMOT), A4.8 (VMOT), A5.8 (VMOT), C2.1, C4.1, C6.1, C8.1, C10.1, C13.1, J11.2, J12.2
A1 DIR: A1.16 (DIR), U1.40 (GPIO2/ADC1_CH1)
A1 MS1: A1.10 (MS1), U1.6 (GPIO6/ADC1_CH5)
A1 MS2: A1.11 (MS2), U1.5 (GPIO5/ADC1_CH4)
A1 MS3: A1.12 (MS3), U1.4 (GPIO4/ADC1_CH3)
A1 STEP: A1.15 (STEP), U1.41 (GPIO1/ADC1_CH0)
A2 DIR: A2.16 (DIR), U1.39 (GPIO42/MTMS)
A2 STEP: A2.15 (STEP), U1.38 (GPIO41/MTDI)
A3 DIR: A3.16 (DIR), U1.37 (GPIO40/MTDO)
A3 STEP: A3.15 (STEP), U1.36 (GPIO39/MTCK)
A4 DIR: A4.16 (DIR), U1.15 (GPIO9/ADC1_CH8)
A4 STEP: A4.15 (STEP), U1.11 (GPIO18/ADC2_CH7)
A5 DIR: A5.16 (DIR), U1.16 (GPIO10/ADC1_CH9)
A5 MS1: A5.10 (MS1), U1.20 (GPIO14/ADC2_CH3)
A5 MS2: A5.11 (MS2), U1.19 (GPIO13/ADC2_CH2)
A5 MS3: A5.12 (MS3), U1.18 (GPIO12/ADC2_CH1)
A5 STEP: A5.15 (STEP), U1.17 (GPIO11/ADC2_CH0)
G MS1: A2.10 (MS1), A3.10 (MS1), A4.10 (MS1), U1.10 (GPIO17/ADC2_CH6)
G MS2: A2.11 (MS2), A3.11 (MS2), A4.11 (MS2), U1.9 (GPIO16/ADC2_CH5/32K_N)
G MS3: A2.12 (MS3), A3.12 (MS3), A4.12 (MS3), U1.8 (GPIO15/ADC2_CH4/32K_P)
GND: A1.1 (GND), A1.7 (GND), A1.9 (~ENABLE), A2.1 (GND), A2.7 (GND), A2.9 (~ENABLE), A3.1 (GND), A3.7 (GND), A3.9 (~ENABLE), A4.1 (GND), A4.7 (GND), A4.9 (~ENABLE), A5.1 (GND), A5.7 (GND), A5.9 (~ENABLE), C1.2, C2.2, C3.2, C4.2, C5.2, C6.2, C7.2, C8.2, C9.2, C10.2, C11.2, C12.2, C13.2, C14.2, J6.3, J7.3, J8.2, J9.2, J10.2, J11.1, J12.1, J13.1, U1.22 (GND), U1.23 (GND), U1.24 (GND), U1.44 (GND)
LS1 NC: J8.1, U1.35 (GPIO38)
LS2 NC: J9.1, U1.27 (GPIO21)
LS3 NC: J10.1, U1.30 (GPIO45)
unnamed: A1.4 (1A), J3.3
unnamed: A1.3 (1B), J3.4
unnamed: A1.5 (2A), J3.2
unnamed: A1.6 (2B), J3.1
unnamed: A1.13 (~RESET), A1.14 (~SLEEP)
unnamed: A2.4 (1A), J1.3
unnamed: A2.3 (1B), J1.4
unnamed: A2.5 (2A), J1.2
unnamed: A2.6 (2B), J1.1
unnamed: A2.13 (~RESET), A2.14 (~SLEEP)
unnamed: A3.4 (1A), J2.3
unnamed: A3.3 (1B), J2.4
unnamed: A3.5 (2A), J2.2
unnamed: A3.6 (2B), J2.1
unnamed: A3.13 (~RESET), A3.14 (~SLEEP)
unnamed: A4.4 (1A), J4.3
unnamed: A4.3 (1B), J4.4
unnamed: A4.5 (2A), J4.2
unnamed: A4.6 (2B), J4.1
unnamed: A4.13 (~RESET), A4.14 (~SLEEP)
unnamed: A5.4 (1A), J5.3
unnamed: A5.3 (1B), J5.4
unnamed: A5.5 (2A), J5.2
unnamed: A5.6 (2B), J5.1
unnamed: A5.13 (~RESET), A5.14 (~SLEEP)
unnamed: C14.1, D1.1 (K), U1.21 (5V)
Servo 1 Signal: J6.1, U1.7 (GPIO7/ADC1_CH6)
Servo 2 Signal: J7.1, U1.12 (GPIO8/ADC1_CH7)

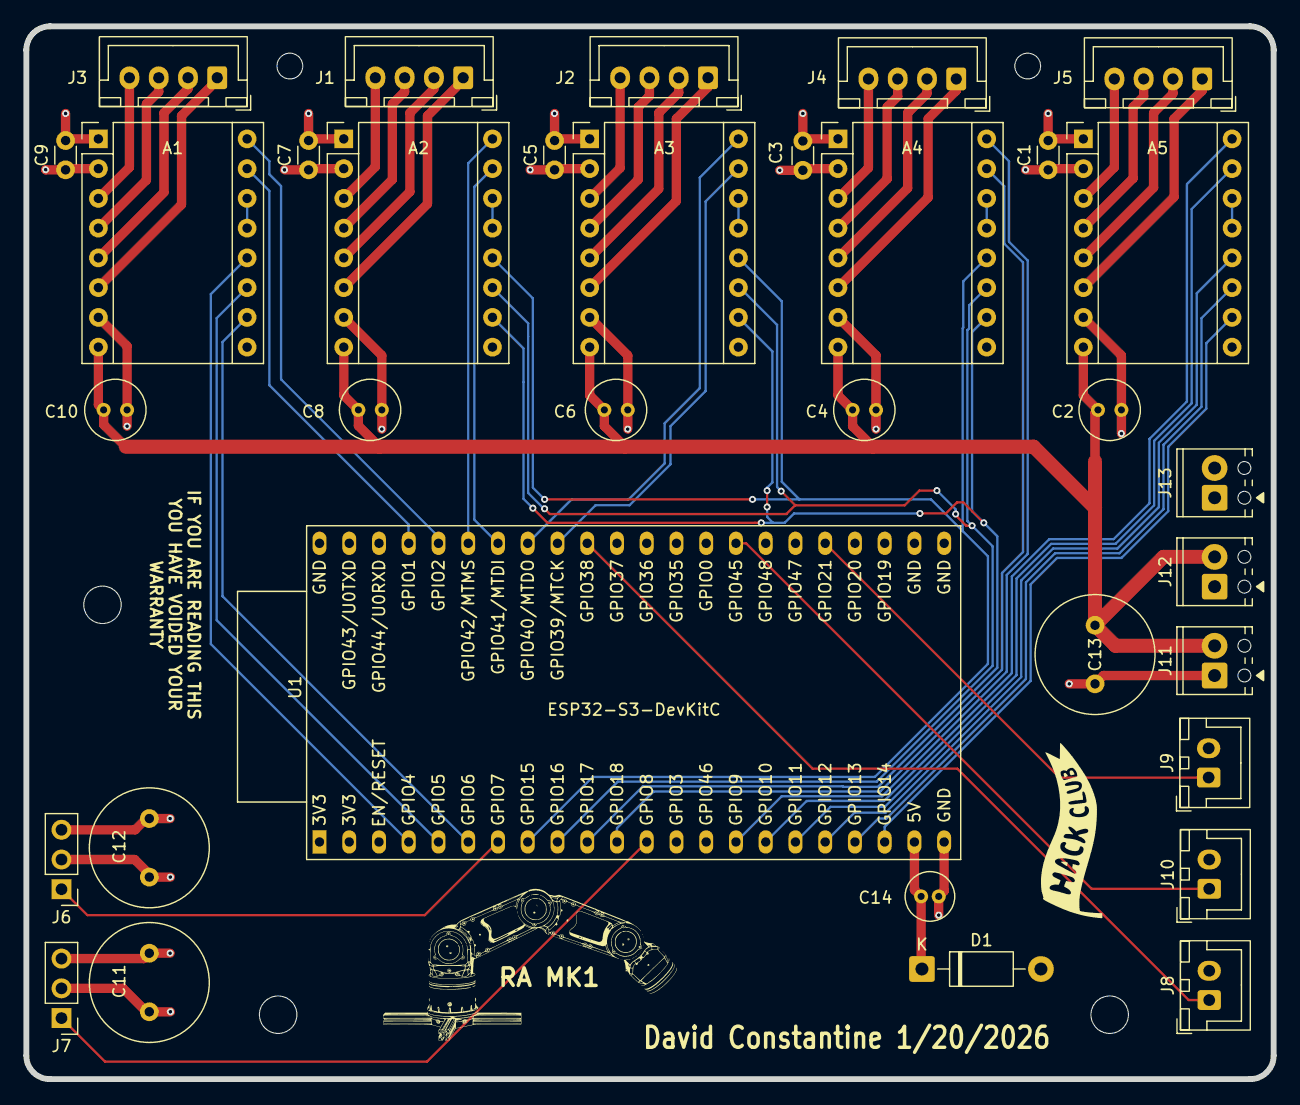
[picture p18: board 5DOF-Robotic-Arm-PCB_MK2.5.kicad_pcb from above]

Board: 4 copper layers, 106.5 x 89.9 mm, 34 parts (0 on the bottom side), 53 nets.

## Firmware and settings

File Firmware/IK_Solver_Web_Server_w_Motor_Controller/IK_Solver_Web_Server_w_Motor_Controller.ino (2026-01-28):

/*
 * Complete 5DOF Robotic Arm Control System
 * ESP32-S3 with IK Solver, Web Interface, and Stepper Control
 * 
 * Features:
 * - Web-based IK solver with visualization
 * - Manual joint control
 * - Stepper motor control with A4988 drivers
 * - Serial terminal interface
 * - Movement confirmation system
 */

#include <Arduino.h>
#include <WiFi.h>
#include <WebServer.h>
#include <math.h>

// WiFi credentials - UPDATE THESE
const char* ssid = "SSID";
const char* password = "PASSWORD";

WebServer server(80);

// Motor pin definitions
struct MotorPins {
  int stepPin;
  int dirPin;
  int ms1Pin;
  int ms2Pin;
  int ms3Pin;
};

MotorPins motor1 = {1, 2, 4, 5, 6};       // Waist
MotorPins motor2 = {41, 42, 17, 16, 15};  // Shoulder
MotorPins motor3 = {39, 40, 17, 16, 15};  // Elbow
MotorPins motor4 = {18, 9, 17, 16, 15};   // Wrist Pitch
MotorPins motor5 = {11, 10, 14, 13, 12};  // Wrist Roll

// Motor configuration
const int STEPS_PER_REV = 200;
const int HARMONIC_RATIO = 25;
int currentMicrosteps[5] = {16, 16, 16, 16, 16};

// Motor speed
const int SPEED_MEDIUM = 1200;

// DH Parameters
const float L1 = 152.5;
const float L2 = 180.0;
const float L3 = 180.0;
const float L4 = 101.0;

// Joint limits
const float JOINT1_MIN = -180.0, JOINT1_MAX = 180.0;
const float JOINT2_MIN = -70.0, JOINT2_MAX = 70.0;
const float JOINT3_MIN = -80.0, JOINT3_MAX = 80.0;
const float JOINT4_MIN = -90.0, JOINT4_MAX = 90.0;
const float JOINT5_MIN = -180.0, JOINT5_MAX = 180.0;

// Joint angles
float theta[5] = {0, 0, 0, 0, 0};
float currentPosition[5] = {0, 0, 0, 0, 0};
float pendingMove[5] = {0, 0, 0, 0, 0};
bool hasPendingMove = false;

// IK solver state
String lastSolveStatus = "Ready";
String lastSolveError = "";
float lastX = 0, lastY = 0, lastZ = 0, lastPitch = 0, lastRoll = 0;

// Serial buffer
String serialBuffer = "";
const int MAX_SERIAL_BUFFER = 5000;

// Motors enabled
bool motorsEnabled = true;

// Forward declarations
bool solveIK(float x, float y, float z, float pitch_deg, float roll_deg);
void handleRoot();
void handleSolve();
void handleStatus();
void handleSerial();
void handleSerialSend();
void handleManualMove();
void handleExecuteMove();
void moveToPosition(float j1, float j2, float j3, float j4, float j5);

void setup() {
  Serial.begin(115200);
  delay(1000);
  
  Serial.println("\n=== 5DOF Robot Arm Control System ===");
  
  // Initialize motors
  initMotor(motor1);
  initMotor(motor2);
  initMotor(motor3);
  initMotor(motor4);
  initMotor(motor5);
  
  setMicrostepping(motor1, 16);
  setMicrostepping(motor2, 16);
  setMicrostepping(motor5, 16);
  
  Serial.println("Motors initialized!");
  
  // Connect to WiFi
  WiFi.begin(ssid, password);
  Serial.print("Connecting to WiFi");
  
  while (WiFi.status() != WL_CONNECTED) {
    delay(500);
    Serial.print(".");
  }
  
  Serial.println("\nWiFi Connected!");
  Serial.print("IP Address: ");
  Serial.println(WiFi.localIP());
  
  // Setup web server routes
  server.on("/", handleRoot);
  server.on("/solve", handleSolve);
  server.on("/status", handleStatus);
  server.on("/serial", handleSerial);
  server.on("/serialSend", HTTP_POST, handleSerialSend);
  server.on("/manualMove", HTTP_POST, handleManualMove);
  server.on("/executeMove", HTTP_POST, handleExecuteMove);
  
  server.begin();
  Serial.println("Web server started!");
  Serial.println("======================================\n");
}

void loop() {
  server.handleClient();
}

void initMotor(MotorPins motor) {
  pinMode(motor.stepPin, OUTPUT);
  pinMode(motor.dirPin, OUTPUT);
  pinMode(motor.ms1Pin, OUTPUT);
  pinMode(motor.ms2Pin, OUTPUT);
  pinMode(motor.ms3Pin, OUTPUT);
  
  digitalWrite(motor.stepPin, LOW);
  digitalWrite(motor.dirPin, LOW);
}

void setMicrostepping(MotorPins motor, int microsteps) {
  switch(microsteps) {
    case 1:
      digitalWrite(motor.ms1Pin, LOW);
      digitalWrite(motor.ms2Pin, LOW);
      digitalWrite(motor.ms3Pin, LOW);
      break;
    case 2:
      digitalWrite(motor.ms1Pin, HIGH);
      digitalWrite(motor.ms2Pin, LOW);
      digitalWrite(motor.ms3Pin, LOW);
      break;
    case 4:
      digitalWrite(motor.ms1Pin, LOW);
      digitalWrite(motor.ms2Pin, HIGH);
      digitalWrite(motor.ms3Pin, LOW);
      break;
    case 8:
      digitalWrite(motor.ms1Pin, HIGH);
      digitalWrite(motor.ms2Pin, HIGH);
      digitalWrite(motor.ms3Pin, LOW);
      break;
    case 16:
      digitalWrite(motor.ms1Pin, HIGH);
      digitalWrite(motor.ms2Pin, HIGH);
      digitalWrite(motor.ms3Pin, HIGH);
      break;
  }
}

long degreesToSteps(float degrees, bool harmonicDrive, int motorIndex) {
  float stepsPerDegree = (STEPS_PER_REV * currentMicrosteps[motorIndex]) / 360.0;
  if (harmonicDrive) stepsPerDegree *= HARMONIC_RATIO;
  return (long)(degrees * stepsPerDegree);
}

void stepMotor(int stepPin) {
  digitalWrite(stepPin, HIGH);
  delayMicroseconds(5);
  digitalWrite(stepPin, LOW);
}

void moveToPosition(float j1, float j2, float j3, float j4, float j5) {
  if (!motorsEnabled) {
    Serial.println("Motors disabled!");
    return;
  }
  
  float targetPos[5] = {j1, j2, j3, j4, j5};
  
  // Calculate steps needed
  long stepsNeeded[5];
  stepsNeeded[0] = degreesToSteps(j1 - currentPosition[0], false, 0);
  stepsNeeded[1] = degreesToSteps(j2 - currentPosition[1], true, 1);
  stepsNeeded[2] = degreesToSteps(j3 - currentPosition[2], true, 2);
  stepsNeeded[3] = degreesToSteps(j4 - currentPosition[3], true, 3);
  stepsNeeded[4] = degreesToSteps(j5 - currentPosition[4], false, 4);
  
  // Set directions
  digitalWrite(motor1.dirPin, stepsNeeded[0] >= 0 ? HIGH : LOW);
  digitalWrite(motor2.dirPin, stepsNeeded[1] >= 0 ? HIGH : LOW);
  digitalWrite(motor3.dirPin, stepsNeeded[2] >= 0 ? HIGH : LOW);
  digitalWrite(motor4.dirPin, stepsNeeded[3] >= 0 ? HIGH : LOW);
  digitalWrite(motor5.dirPin, stepsNeeded[4] >= 0 ? HIGH : LOW);
  
  // Convert to absolute values
  for (int i = 0; i < 5; i++) stepsNeeded[i] = abs(stepsNeeded[i]);
  
  // Find maximum steps
  long maxSteps = 0;
  for (int i = 0; i < 5; i++) {
    if (stepsNeeded[i] > maxSteps) maxSteps = stepsNeeded[i];
  }
  
  // Coordinated movement
  long stepsTaken[5] = {0, 0, 0, 0, 0};
  MotorPins motors[5] = {motor1, motor2, motor3, motor4, motor5};
  
  for (long step = 0; step < maxSteps; step++) {
    for (int i = 0; i < 5; i++) {
      if (stepsTaken[i] * maxSteps < stepsNeeded[i] * step) {
        stepMotor(motors[i].stepPin);
        stepsTaken[i]++;
      }
    }
    delayMicroseconds(SPEED_MEDIUM);
  }
  
  // Update current positions
  for (int i = 0; i < 5; i++) {
    currentPosition[i] = targetPos[i];
  }
  
  Serial.println("Move complete!");
}

bool solveIK(float x, float y, float z, float pitch_deg, float roll_deg) {
  float pitch = pitch_deg * DEG_TO_RAD;
  float roll = roll_deg * DEG_TO_RAD;
  
  theta[0] = atan2(y, x) * RAD_TO_DEG;
  
  float wx = x - L4 * cos(atan2(y, x)) * cos(pitch);
  float wy = y - L4 * sin(atan2(y, x)) * cos(pitch);
  float wz = z - L4 * sin(pitch);
  
  float r = sqrt(wx * wx + wy * wy);
  float h = wz - L1;
  float d = sqrt(r * r + h * h);
  
  if (d > (L2 + L3) || d < abs(L2 - L3)) {
    lastSolveError = "Target out of reach (distance)";
    return false;
  }
  
  float cos_angle2 = (L2 * L2 + d * d - L3 * L3) / (2 * L2 * d);
  if (cos_angle2 < -1.0 || cos_angle2 > 1.0) {
    lastSolveError = "Invalid geometry (shoulder)";
    return false;
  }
  
  float angle2 = acos(cos_angle2);
  float alpha = atan2(h, r);
  
  // Try elbow-up first
  float theta2_up = (alpha + angle2) * RAD_TO_DEG;
  
  float cos_angle3 = (L2 * L2 + L3 * L3 - d * d) / (2 * L2 * L3);
  if (cos_angle3 < -1.0 || cos_angle3 > 1.0) {
    lastSolveError = "Invalid geometry (elbow)";
    return false;
  }
  
  float theta3_up = (PI - acos(cos_angle3)) * RAD_TO_DEG;
  float arm_angle_up = theta2_up - theta3_up;
  float theta4_up = pitch_deg - arm_angle_up;
  
  bool elbowUpValid = (theta2_up >= JOINT2_MIN && theta2_up <= JOINT2_MAX) &&
                      (theta3_up >= JOINT3_MIN && theta3_up <= JOINT3_MAX) &&
                      (theta4_up >= JOINT4_MIN && theta4_up <= JOINT4_MAX);
  
  // Try elbow-down
  float theta2_down = (alpha - angle2) * RAD_TO_DEG;
  float theta3_down = -(PI - acos(cos_angle3)) * RAD_TO_DEG;
  float arm_angle_down = theta2_down - theta3_down;
  float theta4_down = pitch_deg - arm_angle_down;
  
  bool elbowDownValid = (theta2_down >= JOINT2_MIN && theta2_down <= JOINT2_MAX) &&
                        (theta3_down >= JOINT3_MIN && theta3_down <= JOINT3_MAX) &&
                        (theta4_down >= JOINT4_MIN && theta4_down <= JOINT4_MAX);
  
  if (elbowUpValid) {
    theta[1] = theta2_up;
    theta[2] = theta3_up;
    theta[3] = theta4_up;
  } else if (elbowDownValid) {
    theta[1] = theta2_down;
    theta[2] = theta3_down;
    theta[3] = theta4_down;
  } else {
    lastSolveError = "Both elbow configurations exceed joint limits";
    return false;
  }
  
  theta[4] = roll_deg;
  
  for (int i = 0; i < 5; i++) {
    while (theta[i] > 180.0) theta[i] -= 360.0;
    while (theta[i] < -180.0) theta[i] += 360.0;
  }
  
  lastSolveError = "";
  return true;
}

void handleRoot() {
  String html = R"rawliteral(
<!DOCTYPE html>
<html>
<head>
  <meta charset="UTF-8">
  <meta name="viewport" content="width=device-width, initial-scale=1.0">
  <title>5DOF Robot Arm Control</title>
  <style>
    * { margin: 0; padding: 0; box-sizing: border-box; }
    body {
      font-family: 'Roboto', -apple-system, BlinkMacSystemFont, 'Segoe UI', sans-serif;
      background: #121212;
      color: #e0e0e0;
      min-height: 100vh;
      padding: 20px;
    }
    .header {
      background: #1e1e1e;
      border-bottom: 1px solid #2d2d2d;
      padding: 16px 24px;
      margin: -20px -20px 20px -20px;
      display: flex;
      align-items: center;
      gap: 12px;
    }
    .header h1 {
      font-size: 20px;
      font-weight: 500;
      color: #ffffff;
      margin: 0;
    }
    .header-icon {
      width: 32px;
      height: 32px;
      background: #ef5350;
      border-radius: 4px;
      display: flex;
      align-items: center;
      justify-content: center;
      font-size: 18px;
    }
    .main-container {
      max-width: 1200px;
      margin: 0 auto;
    }
    .card {
      background: #2d2d2d;
      border: 1px solid #3d3d3d;
      border-radius: 4px;
      margin-bottom: 16px;
      max-width: 600px;
      overflow: hidden;
    }
    .card-header {
      padding: 16px 20px;
      cursor: pointer;
      display: flex;
      justify-content: space-between;
      align-items: center;
      user-select: none;
      transition: background 0.2s;
    }
    .card-header:hover {
      background: #333333;
    }
    .card-title {
      font-size: 14px;
      font-weight: 500;
      color: #ffffff;
      text-transform: uppercase;
      letter-spacing: 0.5px;
      margin: 0;
    }
    .card-icon {
      font-size: 18px;
      color: #9e9e9e;
      transition: transform 0.3s;
    }
    .card-icon.collapsed {
      transform: rotate(-90deg);
    }
    .card-content {
      padding: 0 20px 20px 20px;
      max-height: 2000px;
      overflow: hidden;
      transition: max-height 0.3s ease-out, padding 0.3s;
    }
    .card-content.collapsed {
      max-height: 0;
      padding: 0 20px;
    }
    .input-grid {
      display: grid;
      grid-template-columns: repeat(auto-fit, minmax(250px, 1fr));
      gap: 16px;
      margin-bottom: 20px;
    }
    .input-group {
      margin-bottom: 16px;
    }
    label {
      display: block;
      font-size: 11px;
      color: #9e9e9e;
      font-weight: 500;
      text-transform: uppercase;
      letter-spacing: 0.5px;
      margin-bottom: 6px;
    }
    .label-with-range {
      display: flex;
      justify-content: space-between;
      align-items: center;
      margin-bottom: 6px;
    }
    .range-info {
      font-size: 10px;
      color: #666;
      font-weight: 400;
      text-transform: none;
    }
    input[type="number"] {
      width: 100%;
      background: #1e1e1e;
      border: 1px solid #3d3d3d;
      border-radius: 4px;
      padding: 8px 10px;
      color: #e0e0e0;
      font-size: 14px;
      transition: all 0.2s;
    }
    input:focus {
      outline: none;
      border-color: #ef5350;
      background: #252525;
    }
    .button-group {
      display: flex;
      gap: 10px;
      margin-top: 16px;
    }
    button {
      padding: 10px 16px;
      border: none;
      border-radius: 4px;
      font-size: 13px;
      font-weight: 500;
      cursor: pointer;
      transition: all 0.2s;
      text-transform: uppercase;
      letter-spacing: 0.5px;
    }
    .btn-primary {
      background: #ef5350;
      color: white;
      flex: 1;
    }
    .btn-primary:hover {
      background: #e53935;
    }
    .btn-secondary {
      background: #3d3d3d;
      color: #e0e0e0;
      border: 1px solid #4d4d4d;
    }
    .btn-secondary:hover {
      background: #4d4d4d;
    }
    .btn-execute {
      background: #66bb6a;
      color: white;
      flex: 1;
    }
    .btn-execute:hover {
      background: #57a05a;
    }
    .btn-execute:disabled {
      background: #3d3d3d;
      color: #666;
      cursor: not-allowed;
    }
    .card.disabled {
      opacity: 0.5;
      pointer-events: none;
    }
    .joint-grid {
      display: grid;
      gap: 10px;
    }
    .joint-item {
      background: #1e1e1e;
      border: 1px solid #3d3d3d;
      border-left: 3px solid #ef5350;
      border-radius: 4px;
      padding: 12px;
      display: flex;
      justify-content: space-between;
      align-items: center;
    }
    .joint-label {
      font-size: 11px;
      color: #9e9e9e;
      text-transform: uppercase;
      letter-spacing: 0.5px;
    }
    .joint-value {
      font-size: 18px;
      font-weight: 500;
      color: #ef5350;
    }
    .joint-control {
      display: grid;
      grid-template-columns: 80px 1fr 80px;
      gap: 8px;
      align-items: center;
      background: #1e1e1e;
      border: 1px solid #3d3d3d;
      border-radius: 4px;
      padding: 12px;
      margin-bottom: 8px;
    }
    .joint-control-label {
      font-size: 11px;
      color: #9e9e9e;
      text-transform: uppercase;
    }
    .joint-control-input {
      display: flex;
      gap: 8px;
      align-items: center;
    }
    .joint-control-input input {
      flex: 1;
      padding: 6px;
      font-size: 13px;
    }
    .joint-control-btn {
      padding: 6px 12px;
      font-size: 12px;
      min-width: 60px;
    }
    .status-bar {
      background: #2d2d2d;
      border: 1px solid #3d3d3d;
      border-radius: 4px;
      padding: 10px 14px;
      display: flex;
      align-items: center;
      gap: 8px;
      font-size: 12px;
    }
    .status-dot {
      width: 8px;
      height: 8px;
      border-radius: 50%;
      background: #4caf50;
      animation: pulse 2s infinite;
    }
    @keyframes pulse {
      0%, 100% { opacity: 1; }
      50% { opacity: 0.5; }
    }
    .status-dot.error {
      background: #ef5350;
    }
    .results-card {
      display: none;
    }
    .results-card.show {
      display: block;
    }
    .error-card {
      background: #2d1515;
      border: 1px solid #5d2020;
      border-left: 3px solid #ef5350;
      border-radius: 4px;
      padding: 14px;
      color: #ef9a9a;
      font-size: 13px;
    }
    .pending-move {
      background: #2d2515;
      border: 1px solid #5d5020;
      border-left: 3px solid #ffa726;
      border-radius: 4px;
      padding: 14px;
      color: #ffb74d;
      font-size: 13px;
      margin-bottom: 16px;
    }
    .math-section {
      margin-bottom: 20px;
    }
    .math-section:last-child {
      margin-bottom: 0;
    }
    .math-title {
      color: #ef5350;
      font-size: 13px;
      font-weight: 600;
      margin-bottom: 8px;
      text-transform: uppercase;
      letter-spacing: 0.5px;
    }
    .math-line {
      font-family: 'Courier New', monospace;
      color: #b0b0b0;
      font-size: 13px;
      line-height: 1.8;
      padding: 4px 0;
    }
    .math-var {
      color: #66bb6a;
    }
    .math-result {
      color: #ef5350;
      font-weight: 600;
    }
    .math-comment {
      color: #666;
      font-style: italic;
      margin-left: 10px;
    }
    .math-error {
      background: #2d1515;
      border-left: 3px solid #ef5350;
      padding: 12px;
      margin: 8px 0;
      color: #ef9a9a;
      border-radius: 4px;
    }
    .math-warning {
      background: #2d2515;
      border-left: 3px solid #ffa726;
      padding: 12px;
      margin: 8px 0;
      color: #ffb74d;
      border-radius: 4px;
    }
    .terminal {
      background: #0d0d0d;
      border: 1px solid #3d3d3d;
      border-radius: 4px;
      padding: 12px;
      font-family: 'Courier New', monospace;
      font-size: 13px;
      color: #00ff00;
      height: 300px;
      overflow-y: auto;
      margin-bottom: 12px;
      white-space: pre-wrap;
      word-wrap: break-word;
    }
    .terminal-input-group {
      display: flex;
      gap: 8px;
    }
    .terminal-input {
      flex: 1;
      background: #1e1e1e;
      border: 1px solid #3d3d3d;
      border-radius: 4px;
      padding: 10px;
      color: #00ff00;
      font-family: 'Courier New', monospace;
      font-size: 13px;
    }
    .terminal-input:focus {
      outline: none;
      border-color: #ef5350;
    }
    .btn-terminal {
      background: #2d2d2d;
      color: #00ff00;
      border: 1px solid #3d3d3d;
      padding: 10px 20px;
      border-radius: 4px;
      cursor: pointer;
      font-family: 'Courier New', monospace;
      font-size: 13px;
      transition: background 0.2s;
    }
    .btn-terminal:hover {
      background: #3d3d3d;
    }
  </style>
</head>
<body>
  <div class="header">
    <div class="header-icon">🦾</div>
    <h1>Robot Arm Control System</h1>
  </div>
  
  <div class="main-container">
    <div class="card">
      <div class="card-header" onclick="toggleCard(this)">
        <div class="card-title">Current Position</div>
        <div class="card-icon">▼</div>
      </div>
      <div class="card-content">
        <div class="joint-grid">
          <div class="joint-item">
            <div class="joint-label">Joint 1 (Base)</div>
            <div class="joint-value" id="currentJ1">0.00°</div>
          </div>
          <div class="joint-item">
            <div class="joint-label">Joint 2 (Shoulder)</div>
            <div class="joint-value" id="currentJ2">0.00°</div>
          </div>
          <div class="joint-item">
            <div class="joint-label">Joint 3 (Elbow)</div>
            <div class="joint-value" id="currentJ3">0.00°</div>
          </div>
          <div class="joint-item">
            <div class="joint-label">Joint 4 (Wrist Pitch)</div>
            <div class="joint-value" id="currentJ4">0.00°</div>
          </div>
          <div class="joint-item">
            <div class="joint-label">Joint 5 (Wrist Roll)</div>
            <div class="joint-value" id="currentJ5">0.00°</div>
          </div>
        </div>
      </div>
    </div>
    
    <div class="card">
      <div class="card-header" onclick="toggleCard(this)">
        <div class="card-title">Manual Joint Control</div>
        <div class="card-icon">▼</div>
      </div>
      <div class="card-content">
        <div class="joint-control">
          <div class="joint-control-label">Joint 1</div>
          <div class="joint-control-input">
            <input type="number" id="manual1" value="0" step="1">
            <span style="color:#666">°</span>
          </div>
          <button class="btn-secondary joint-control-btn" onclick="moveJoint(0)">Move</button>
        </div>
        <div class="joint-control">
          <div class="joint-control-label">Joint 2</div>
          <div class="joint-control-input">
            <input type="number" id="manual2" value="0" step="1">
            <span style="color:#666">°</span>
          </div>
          <button class="btn-secondary joint-control-btn" onclick="moveJoint(1)">Move</button>
        </div>
        <div class="joint-control">
          <div class="joint-control-label">Joint 3</div>
          <div class="joint-control-input">
            <input type="number" id="manual3" value="0" step="1">
            <span style="color:#666">°</span>
          </div>
          <button class="btn-secondary joint-control-btn" onclick="moveJoint(2)">Move</button>
        </div>
        <div class="joint-control">
          <div class="joint-control-label">Joint 4</div>
          <div class="joint-control-input">
            <input type="number" id="manual4" value="0" step="1">
            <span style="color:#666">°</span>
          </div>
          <button class="btn-secondary joint-control-btn" onclick="moveJoint(3)">Move</button>
        </div>
        <div class="joint-control">
          <div class="joint-control-label">Joint 5</div>
          <div class="joint-control-input">
            <input type="number" id="manual5" value="0" step="1">
            <span style="color:#666">°</span>
          </div>
          <button class="btn-secondary joint-control-btn" onclick="moveJoint(4)">Move</button>
        </div>
        <div class="button-group">
          <button class="btn-secondary" onclick="homeAll()">Home All</button>
          <button class="btn-secondary" onclick="updateManualFromCurrent()">Sync Values</button>
        </div>
      </div>
    </div>
    
    <div class="card">
      <div class="card-header" onclick="toggleCard(this)">
        <div class="card-title">IK Solver - Target Position</div>
        <div class="card-icon">▼</div>
      </div>
      <div class="card-content">
        <div class="input-grid">
          <div class="input-group">
            <div class="label-with-range">
              <label>X Position (mm)</label>
              <span class="range-info">Max reach ~360 mm</span>
            </div>
            <input type="number" id="x" step="0.01" value="200">
          </div>
          
          <div class="input-group">
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

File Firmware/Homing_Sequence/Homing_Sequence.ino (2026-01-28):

/*
 * Homing and Park Sequence for 5DOF Robot Arm
 * 
 * Limit Switches:
 * - Limit SW 1 (GPIO 38): Joint 2 (Shoulder)
 * - Limit SW 2 (GPIO 21): Joint 3 (Elbow)
 * - Limit SW 3 (GPIO 45): Joint 4 (Wrist Pitch)
 * 
 * Homing Strategy:
 * - Move each axis slowly until limit switch triggers
 * - Back off slightly to clear the switch
 * - Set that position as the home/zero position
 * - After homing, move to park position (X=350, Y=0, Z=350)
 */

#include <Arduino.h>

// Motor pin definitions
struct MotorPins {
  int stepPin;
  int dirPin;
  int ms1Pin;
  int ms2Pin;
  int ms3Pin;
};

MotorPins motor1 = {1, 2, 4, 5, 6};       // Waist
MotorPins motor2 = {41, 42, 17, 16, 15};  // Shoulder
MotorPins motor3 = {39, 40, 17, 16, 15};  // Elbow
MotorPins motor4 = {18, 9, 17, 16, 15};   // Wrist Pitch
MotorPins motor5 = {11, 10, 14, 13, 12};  // Wrist Roll

// Limit switches
const int LIMIT_SW1 = 38;  // Joint 2 - Shoulder
const int LIMIT_SW2 = 21;  // Joint 3 - Elbow
const int LIMIT_SW3 = 45;  // Joint 4 - Wrist Pitch

// Motor configuration
const int STEPS_PER_REV = 200;
const int HARMONIC_RATIO = 25;
int currentMicrosteps[5] = {16, 16, 16, 16, 16};

// Motor speeds (microseconds between steps)
const int SPEED_HOMING = 2500;    // Slow speed for homing
const int SPEED_BACKOFF = 1500;   // Medium speed for backing off
const int SPEED_NORMAL = 1200;    // Normal movement speed

// DH Parameters
const float L1 = 152.5;
const float L2 = 180.0;
const float L3 = 180.0;
const float L4 = 101.0;

// Joint limits
const float JOINT1_MIN = -180.0, JOINT1_MAX = 180.0;
const float JOINT2_MIN = -70.0, JOINT2_MAX = 70.0;
const float JOINT3_MIN = -80.0, JOINT3_MAX = 80.0;
const float JOINT4_MIN = -90.0, JOINT4_MAX = 90.0;
const float JOINT5_MIN = -180.0, JOINT5_MAX = 180.0;

// Current positions
float currentPosition[5] = {0, 0, 0, 0, 0};

// Homing status
bool isHomed = false;

void setup() {
  Serial.begin(115200);
  delay(1000);
  
  Serial.println("\n=== 5DOF Robot Arm Homing System ===");
  
  // Initialize motors
  initMotor(motor1);
  initMotor(motor2);
  initMotor(motor3);
  initMotor(motor4);
  initMotor(motor5);
  
  setMicrostepping(motor1, 16);
  setMicrostepping(motor2, 16);
  setMicrostepping(motor5, 16);
  
  // Initialize limit switches
  pinMode(LIMIT_SW1, INPUT_PULLUP);
  pinMode(LIMIT_SW2, INPUT_PULLUP);
  pinMode(LIMIT_SW3, INPUT_PULLUP);
  
  Serial.println("Motors and limit switches initialized!");
  Serial.println("Commands:");
  Serial.println("  H - Home all axes with limit switches");
  Serial.println("  P - Park at safe position (X=350, Y=0, Z=350)");
  Serial.println("  S - Check limit switch status");
  Serial.println("========================================\n");
}

void loop() {
  if (Serial.available() > 0) {
    char cmd = Serial.read();
    
    switch(cmd) {
      case 'H':
      case 'h':
        homeAllAxes();
        break;
        
      case 'P':
      case 'p':
        if (!isHomed) {
          Serial.println("ERROR: Must home first! Send 'H' command.");
        } else {
          parkPosition();
        }
        break;
        
      case 'S':
      case 's':
        checkLimitSwitches();
        break;
    }
    
    while (Serial.available() > 0) Serial.read();
  }
}

void initMotor(MotorPins motor) {
  pinMode(motor.stepPin, OUTPUT);
  pinMode(motor.dirPin, OUTPUT);
  pinMode(motor.ms1Pin, OUTPUT);
  pinMode(motor.ms2Pin, OUTPUT);
  pinMode(motor.ms3Pin, OUTPUT);
  
  digitalWrite(motor.stepPin, LOW);
  digitalWrite(motor.dirPin, LOW);
}

void setMicrostepping(MotorPins motor, int microsteps) {
  switch(microsteps) {
    case 16:
      digitalWrite(motor.ms1Pin, HIGH);
      digitalWrite(motor.ms2Pin, HIGH);
      digitalWrite(motor.ms3Pin, HIGH);
      break;
    default:
      digitalWrite(motor.ms1Pin, HIGH);
      digitalWrite(motor.ms2Pin, HIGH);
      digitalWrite(motor.ms3Pin, HIGH);
  }
}

void stepMotor(int stepPin, int delayTime) {
  digitalWrite(stepPin, HIGH);
  delayMicroseconds(5);
  digitalWrite(stepPin, LOW);
  delayMicroseconds(delayTime);
}

void checkLimitSwitches() {
  Serial.println("\n=== Limit Switch Status ===");
  Serial.print("Joint 2 (Shoulder): ");
  Serial.println(digitalRead(LIMIT_SW1) == LOW ? "TRIGGERED" : "Open");
  Serial.print("Joint 3 (Elbow):    ");
  Serial.println(digitalRead(LIMIT_SW2) == LOW ? "TRIGGERED" : "Open");
  Serial.print("Joint 4 (Wrist):    ");
  Serial.println(digitalRead(LIMIT_SW3) == LOW ? "TRIGGERED" : "Open");
  Serial.println("===========================\n");
}

void homeAllAxes() {
  Serial.println("\n╔════════════════════════════════════╗");
  Serial.println("║   HOMING SEQUENCE INITIATED        ║");
  Serial.println("╚════════════════════════════════════╝\n");
  
  // Check initial switch states
  Serial.println("Checking initial limit switch states...");
  checkLimitSwitches();
  
  // Home Joint 2 (Shoulder)
  Serial.println("─────────────────────────────────────");
  Serial.println("Homing Joint 2 (Shoulder)...");
  homeAxisWithLimitSwitch(motor2, LIMIT_SW1, 1, 2, true);  // Move towards negative (assume switch at min)
  
  delay(500);
  
  // Home Joint 3 (Elbow)
  Serial.println("─────────────────────────────────────");
  Serial.println("Homing Joint 3 (Elbow)...");
  homeAxisWithLimitSwitch(motor3, LIMIT_SW2, 2, 3, true);  // Move towards negative
  
  delay(500);
  
  // Home Joint 4 (Wrist Pitch)
  Serial.println("─────────────────────────────────────");
  Serial.println("Homing Joint 4 (Wrist Pitch)...");
  homeAxisWithLimitSwitch(motor4, LIMIT_SW3, 3, 4, true);  // Move towards negative
  
  // Set homed positions
  // Assuming limit switches are at negative extremes
  currentPosition[1] = JOINT2_MIN;  // Shoulder at -70°
  currentPosition[2] = JOINT3_MIN;  // Elbow at -80°
  currentPosition[3] = JOINT4_MIN;  // Wrist at -90°
  
  Serial.println("─────────────────────────────────────");
  Serial.println("\n✓ HOMING COMPLETE!");
  Serial.println("Current positions set:");
  Serial.printf("  Joint 2 (Shoulder): %.2f°\n", currentPosition[1]);
  Serial.printf("  Joint 3 (Elbow):    %.2f°\n", currentPosition[2]);
  Serial.printf("  Joint 4 (Wrist):    %.2f°\n", currentPosition[3]);
  
  isHomed = true;
  
  Serial.println("\n✓ Ready to move! Send 'P' to park.\n");
}
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

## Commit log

2026-01-09 Update README with current progress section
    Added a section for current progress and included an image.
2026-01-09 Revise README for project progress and motor issues
    Updated README with current progress and motor limitations.
2026-01-09 Fix image links and add stepper motor image
    Updated image references and added a new image for the stepper motors.
2026-01-09 Revise motor torque details and upgrade intentions
    Updated torque specifications and future plans for motor upgrades.
2026-01-09 Change project from 6DOF to 5DOF Robotic Arm
    Updated project title and description to reflect 5DOF.
2026-01-11 Added BOM
    [5DOF-Robotic-Arm BOM - Sheet1.csv]
2026-01-11 Rename BOM file to 5DOF-Robotic-Arm_BOM.csv
    [5DOF-Robotic-Arm_BOM.csv]
2026-01-11 Update and rename 5DOF-Robotic-Arm_BOM.csv to BOM/5DOF-Robotic-Arm_BOM.csv
    [5DOF-Robotic-Arm_BOM.csv]
2026-01-11 Rename BOM file to 5DOF-Robotic-Arm_BOMcsv
2026-01-11 Rename BOM file to correct CSV extension
    [5DOF-Robotic-Arm_BOM.csv]
2026-01-11 Rename BOM file for 5DOF Robotic Arm
    [5DOF-Robotic-Arm_BOM.csv]
2026-01-11 Rename Screenshot 2026-01-11 173757.png to Wiring/Wiring-Diagram.png
2026-01-13 Revise journal entries for Voron project updates
    Updated journal entries to reflect recent progress and excitement about the Voron 3D printer.
2026-01-14 Revise journal backlog with recent updates and images
    Updated journal backlog with new entries and images detailing the progress on the arm design and printing process.
2026-01-25 Update and rename 5DOF-Robotic-Arm BOM - BOM (1).csv to 5DOF-Robotic-Arm BOM - BOM.csv
    [5DOF-Robotic-Arm BOM - BOM.csv]
2026-01-25 Add PCB section to README with images
    Added PCB section with schematic, footprint, and render images.
2026-01-26 Enhance BOM with Total Price column
    Added total price column to BOM for better cost tracking.
2026-01-26 Fix typos in BOM section of README.md
2026-01-27 Update and rename PCB Pin Assignments - PCB Pin Assignments.csv to PCB Pin Assignments.csv
    [PCB Pin Assignments.csv]
2026-01-27 Clarify PCB installation requirements in README
    Updated the description of the 5DOF Arm, clarifying installation requirements for the PCB and motors.
2026-01-28 Update README with credit and design link
    Added credit and link to original Strain-Wave Gearbox design.
2026-01-28 Update image in README for 5DOF Robotic Arm
2026-01-28 Update strain wave gearbox credit in README
    Added more details about the strain wave gearbox credit.
2026-01-28 Update BACKLOG.md with new journal entries
    Added new journal entries detailing progress on shoulder design and 3D printing updates.
2026-01-28 Revise BACKLOG.md for Upper Arm design updates
    Refined the description of the Upper Arm design and updated the text for clarity. Fixed minor grammatical errors and improved the flow of the narrative.
2026-01-28 Update README with new images and BOM section
    Added multiple images and a BOM section to the README.
2026-01-28 Replace WiFi credentials with placeholders
    Updated WiFi credentials to placeholders for security.
    [IK_Solver_Web_Server_w_Motor_Controller.ino]
2026-02-08 Revise BOM table with updated price details
    Updated BOM table to reflect changes in total price for items.
2026-02-17 Update and rename 5DOF-Robotic-Arm BOM - BOM.csv to BOM.csv
    [BOM.csv]
2026-02-17 Add links to BOM items in README
    Updated the BOM table to include links for each item.
2026-02-17 Add usage instructions for the 5DOF Arm project
    Added a section on usage instructions for the 5DOF Arm project, detailing setup and control mechanisms.
2026-02-17 Update price for 0.1uF capacitor in README
    Updated the price for the 0.1uF capacitor to reflect the new cost.
